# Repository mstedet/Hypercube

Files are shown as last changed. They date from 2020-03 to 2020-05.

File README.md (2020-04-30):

# Metalværksted Seniorhus Odense 3D printer  
## Baseret på Scott Alford's [HyperCube Evolution](https://www.thingiverse.com/thing:2254103)  

# Matrialer:
## [Item Aluminiumsprofiler 3030 and 2020 extrusion](https://www.linearmodul.dk/sida5_dk.html)
15 Meter [Profil 6 30x30 leicht, natur](https://product.item24.de/directlink/de/pro/41906)  
Profil 6 30x30 Let  
  * 4 stk 1500mm  
  * 10 stk 490mm  

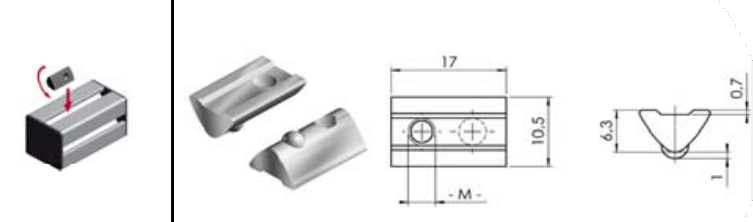
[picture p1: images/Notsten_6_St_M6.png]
Notsten 6 St M6
150 x [Notsten 6 St M6](https://www.linearmodul.dk/)   
50 x  Notsten Not 5, M5 svingbar m.skaft St.FZB  

100 x [Standard-Fastening Set 6 E, bright zinc-plated](https://product.item24.de/produkte/produktkatalog/produktdetails/products/standard-verbindungssaetze-1001012015/standard-verbindungssatz-6-e-verzinkt-64865/)   
 - Profil 6 30x30 Let kobling  
### item Konstruktionsprofile 5
[3 meter Profil 5 20x20, natur 0.0.370.03](https://product.item24.de/produkte/produktkatalog/produktdetails/products/konstruktionsprofile-5-1001042368/profil-5-20x20-natur-37003/)  
  
  * 2 stk 400mm  
  * 2 stk 440mm

## Bolte 
###  Button head screw, DIN EN ISO 7380-1  
   

#### M6
500 stk M6x12   

### DIN 912 ISO 4762 - Hexagon socket Head Cap Screws
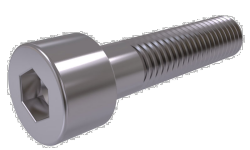
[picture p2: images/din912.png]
DIN 912
 
#### M5
8 stk M5x10, for Trapezewagon  
12 stk M5x10,  for Z-Axel Bearing  
#### M3
8 stk M3 x 10mm, for Z-Motor_Holder  
8 stk M3 x 12mm, for Trapezewagon  
24 stk M3 x 25mm, for Z-Axel Bearing  
8 stk M3 x 25mm, for Z-Axel Bracket

### DIN 965, SKRUE MED UNDERSÆNKET HOVED MED H-KRYDSKÆRV  
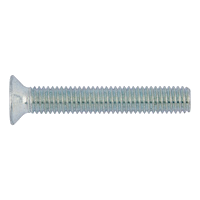
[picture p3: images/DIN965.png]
DIN965

#### M4
4 stk M4 x 50mm, for heatbed leveling 
## Møtriker
48 stk M3

## Axeler 
1 Meter [Aksel ø8  h6 - Hærdet & slebet dia.  8 mm (HL=6m)](https://www.linearmodul.dk/)  
1 Meter [Aksel ø10 h6 - hærdet & slebet dia. 10 mm (HL=6m)](https://www.linearmodul.dk/)  
4 Meter [Aksel ø12 h6 - hærdet & slebet dia. 12 mm (HL=6m)](https://www.linearmodul.dk/)  

## Motors
5 x [NEMA 17 42mm Stepper Motors](https://www.amazon.de/gp/product/B07STSYWY6/ref=ppx_yo_dt_b_asin_title_o08_s00?ie=UTF8&psc=1)  
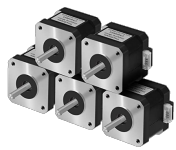
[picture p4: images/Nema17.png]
nema17


## Lead Screw M8 
2 x [Leitspindel+CopperMutter+VertikallagerLager+Kupplung (1Set)](https://www.amazon.de/gp/product/B07LDZPSKL/ref=ppx_yo_dt_b_asin_title_o06_s02?ie=UTF8&psc=1)  
[her er andre modeller fra aliexpress.com](https://www.aliexpress.com/item/32507277503.html?spm=a2g0o.cart.0.0.331e3c00jh9G45&mp=1) 
  
eller   

2 x [CNC 3D Printer THSL-300-8D Trapezoidal Rod T8 Lead Screw Thread 8mm Lead 1mm Length 600mm with Brass Nut](https://www.aliexpress.com/item/32507277503.html?spm=a2g0o.cart.0.0.590f3c00qjklE0&mp=1)  
4 x [KP08 Bearing Shaft Support Spherical Roller Zinc Alloy Mounted Bearings Pillow Block Housing](https://www.aliexpress.com/item/32571310602.html?spm=a2g0o.cart.0.0.590f3c00qjklE0&mp=1)  
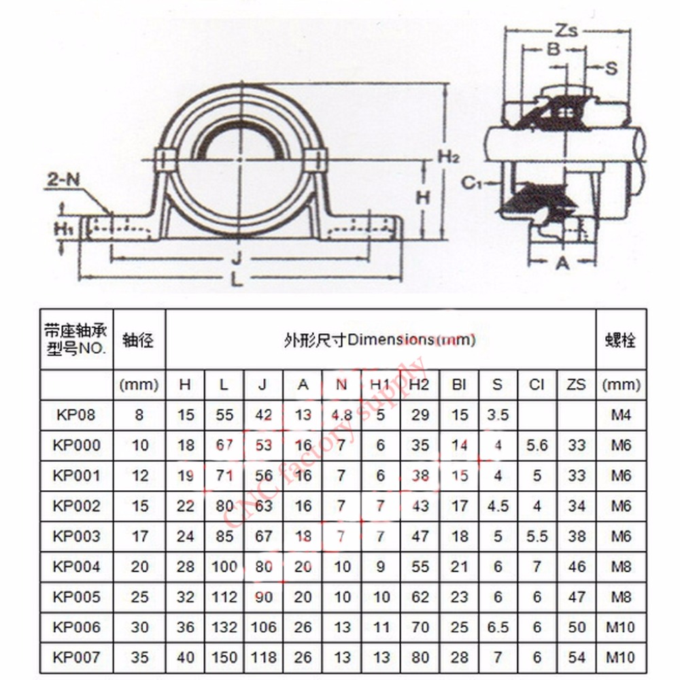
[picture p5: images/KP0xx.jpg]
KP0xx
  

## Pulleys and Belts
5m Polyurethane GT2 6mm belt &   
2 x [GT2 Timing Pulley (20 teeth) 5mm bore for 6mm belt](https://www.amazon.de/gp/product/B06XKVX3FY/ref=ppx_yo_dt_b_asin_title_o08_s00?ie=UTF8&psc=1)  
6 x [GT2 Idler Pulley (20 teeth) 3mm bore](https://www.amazon.de/gp/product/B07K8FNGCZ/ref=ppx_yo_dt_b_asin_title_o06_s01?ie=UTF8&psc=1)  
2 x [GT2 Idler Pulley without teeth (20 teeth) 3mm bore](https://www.amazon.de/gp/product/B083RCTF7T/ref=ppx_yo_dt_b_asin_title_o05_s00?ie=UTF8&psc=1)  

## Linear Bearings  
8 x LM12UU 12mm Linear Ball Bearings  eller [Linear Ball Bearings LM12LUU 12 Part Bush Bushing 3D Printers Parts Aluminum Accessories](https://www.aliexpress.com/item/4000586376717.html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,searchweb201602_,searchweb201603_)  
4 x LM10UU 10mm Linear Ball Bearings or 2 x LM10LUU 10mm Long Linear Ball Bearings  
4 x LM8UU 8mm Linear Ball Bearings  

## Heated Bed components
1 x [Print Bed Rubber Heater 408 x 408 mm](https://3dstore.dk/tilbehoer/reservedele/creality-3d/cr10s/print-bed-rubber-heater-408-x-408-mm/)  
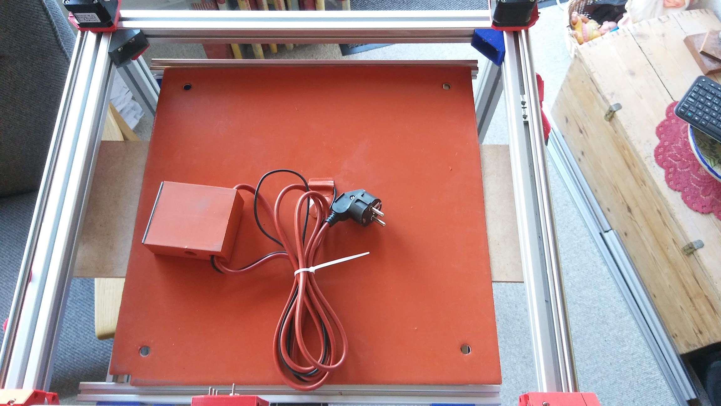
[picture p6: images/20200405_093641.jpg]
Heated Bed
  
1 x [PrimaCreator FlexPlate PEI 410 x 410 mm](https://3dstore.dk/tilbehoer/print-surface/primacreator-flexplate-pei-410-x-410-mm/)  
1 x Aluplate 430x430x3 mm  
1 x Flex pe coated plade - MGLo63.00.15 P1908084  
1 x [Hvid Magnetfolie. Selvklæbende. 50 cm](https://www.boxdelux.dk/shop/hvid-magnetfolie-selvklaebende-20277p.html)  
10 x [Type A - Hot bed platform leveling spring length 25mm outer diameter 10mm ID 5mm ](https://www.aliexpress.com/item/33001295923.html?spm=a2g0s.9042311.0.0.26194c4dYd3kvQ)
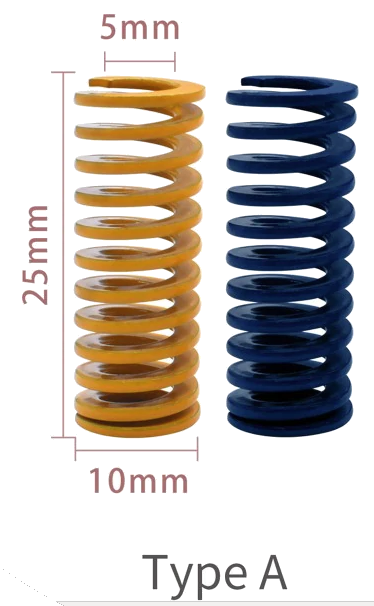
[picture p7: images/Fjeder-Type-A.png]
Fjedr-Type-A


## HotEnd:
1 x [E3D v6 HotEnd Full Kit - 1.75mm Bowden (24v)](https://filament23d.dk/e3d-v6-hotend-full-kit-1-75mm-bowden-24v-da.html) - **[Assembly Guid](https://wiki.e3d-online.com/E3D-v6_Assembly)**  
1 x [24V Blow 50mm](https://filament23d.dk/24v-blow-50mm-da.html)  
1 x [Extruder](https://www.amazon.de/gp/product/B07TJ8PB7D/ref=ppx_yo_dt_b_asin_title_o07_s00?ie=UTF8&psc=1  eller 
1 x [Aluminum Upgrade Dual Gear Mk8 Extruder for Extruder CR10 CR-10S PRO RepRap 1.75mm 3D Parts Drive Feed double pulley](https://www.aliexpress.com/item/4000103596931.html?spm=a2g0s.9042311.0.0.26194c4dYd3kvQ)  
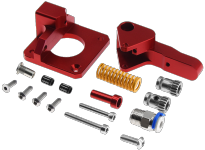
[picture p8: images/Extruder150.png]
Extruder


)  
10 stk [POWER MAGNET, SKIVE 12X6 MM](https://www.magnetz.dk/power-magnet-skive-12x6-mm)

## Control System
1 x [24V 400W power supply](https://www.amazon.de/gp/product/B01G257UHW/ref=ppx_yo_dt_b_asin_title_o02_s00?ie=UTF8&psc=1)  
1 x [BIGTREETECH-SKR-V1.4](https://github.com/bigtreetech/BIGTREETECH-SKR-V1.3/tree/master/BTT%20SKR%20V1.4)  
1 x [BIGTREETECH-TFT35-V3.0](https://github.com/bigtreetech/BIGTREETECH-TFT35-V3.0)  
1 x [BIGTREETECH-MINI-UPS-V2.0](https://github.com/bigtreetech/BIGTREETECH-MINI-UPS-V2.0/tree/master/BTT%20UPS%2024V%20V1.0)  
5 X [BIGTREETECH-TMC2130-V3.0](https://github.com/bigtreetech/BIGTREETECH-TMC2130-V3.0)  
1 x [ESP-01S WIFI Module ESP8266 For SKR](https://www.biqu.equipment/products/esp-01s-wifi-module-esp8266-for-skr-pro)  

# 3D-Printede Dele: 
## Filament:
2 x [Spectrum Filaments – PLA – 1.75mm – Deep Black – 1 kg](https://3dstore.dk/filament/spectrum-filaments-pla-1-75mm-deep-black-1-kg/)  
2 x [Spectrum Filaments – PLA – 1.75mm – Dark Grey – 1 kg](https://3dstore.dk/filament/spectrum-filaments-pla-1-75mm-dark-grey-1-kg/)  
2 x [Spectrum Filaments – PLA – 1.75mm – Navy Blue – 1 kg](https://3dstore.dk/filament/spectrum-filaments-pla-1-75mm-navy-blue-1-kg/)  
2 x [Spectrum Filaments – PLA – 1.75mm – Bloody Red – 1 kg](https://3dstore.dk/filament/spectrum-filaments-pla-1-75mm-bloody-red-1-kg/)  
## PrintaFix:
3 x [APRINTAPRO PrintaFix Basic 100ml](https://3dstore.dk/tilbehoer/printafix/aprintapro-printafix-basic/)  
## Filer:
* [FreeCad (FCStd) filer & STL filer kan hentest her](https://github.com/mstedet/Hypercube/tree/master/FreeCad)  
## 3030 Profiler
4 x EndCap_3030 - **[STL-fil](/FreeCad/3030/EndCap_3030.stl)** - **[FreeCad-fil](/FreeCad/3030/EndCap_3030.FCStd)**
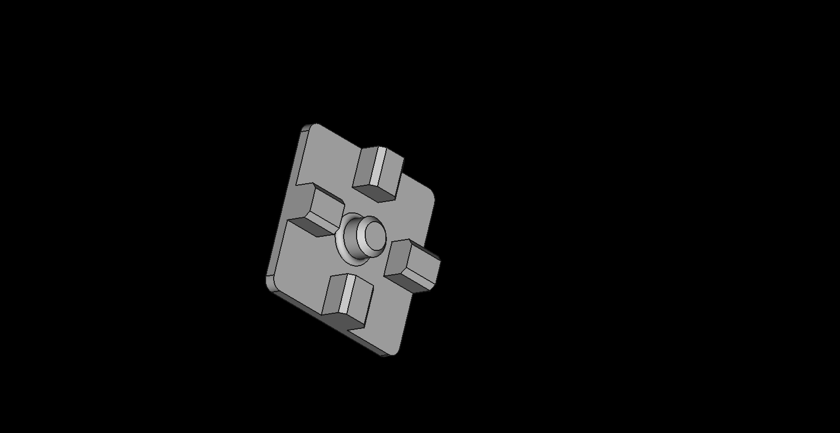
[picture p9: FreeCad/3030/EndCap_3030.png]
EndCap_3030
 
4 x FodBund 3030 - **[STL-fil](/FreeCad/3030/Foot-30a.stl)** - **[FreeCad-fil](/FreeCad/3030/Foot-30a.FCStd)**
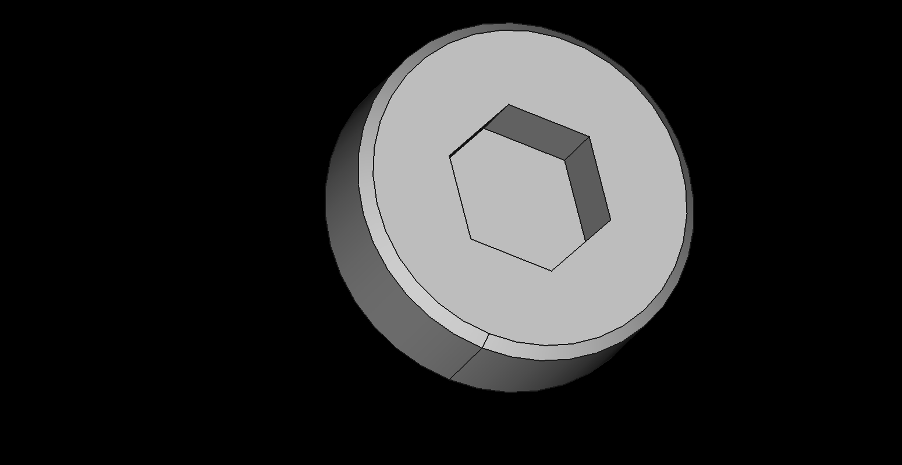
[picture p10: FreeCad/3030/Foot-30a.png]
FodBund
 
4 x FodJustermøtrik - **[STL-fil](/FreeCad/3030/Foot-30b.stl)** - **[FreeCad-fil](/FreeCad/3030/Foot-30b.FCStd)**
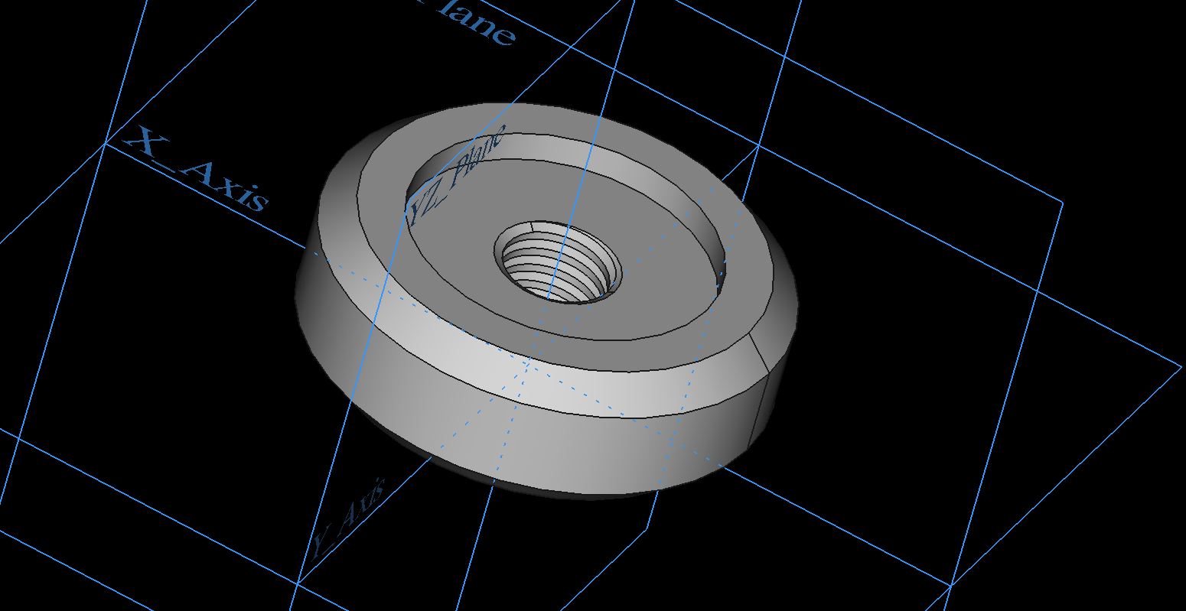
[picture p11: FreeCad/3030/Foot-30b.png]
FodJustermøtrik
 

## X-Axel
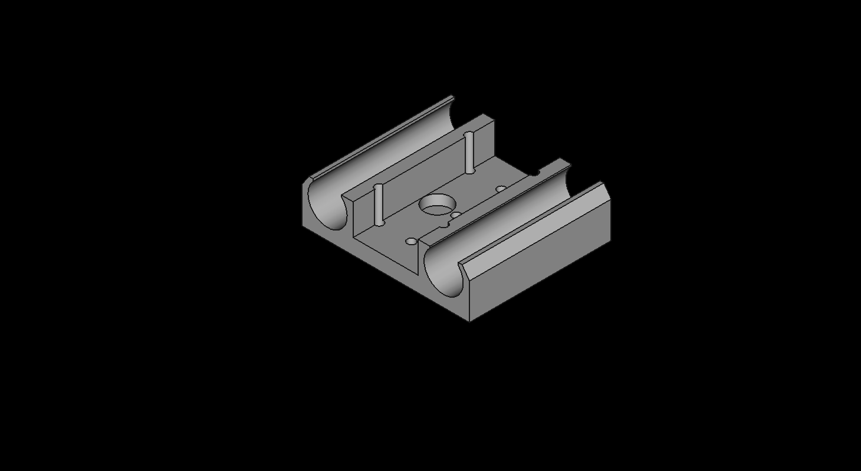
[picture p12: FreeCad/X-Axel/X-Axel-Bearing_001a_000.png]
X-Axel-Bearing_A
1 x X-Axel-Bearing_A   
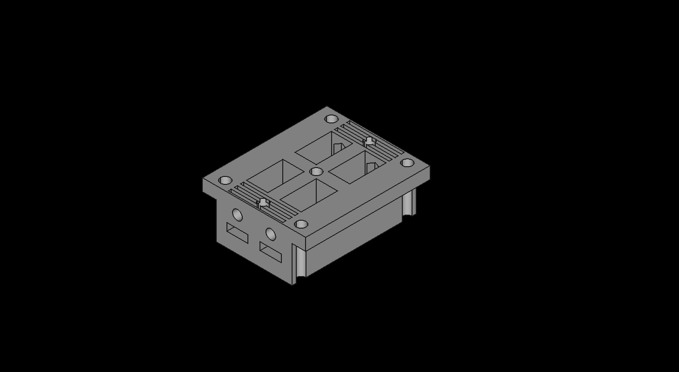
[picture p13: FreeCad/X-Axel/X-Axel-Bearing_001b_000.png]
X-Axel-Bearing_B
1 x X-Axel-Bearing_B   
2 x X-Axel-Belt-Tension  
1 x X-Axel-Printhead-Base

## Y-Axel
2 x Afstandstykke_2mm - **[STL-fil](/FreeCad/Y-Axel/Afstandstykke_2mm/Afstandstykke_2mm.stl)** - **[FreeCad-fil](/FreeCad/Y-Axel/Afstandstykke_2mm/Afstandstykke_2mm.FCStd)**
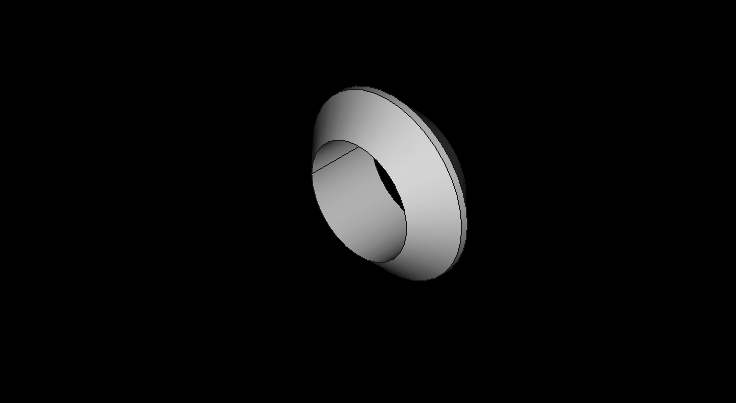
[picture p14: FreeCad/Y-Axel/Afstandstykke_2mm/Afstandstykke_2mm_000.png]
Afstandstykke
  
2 x Y-Axel-Bearing_A - **[STL-fil](FreeCad/Y-Axel/Y-Axel-Bearing_007/Y-Axel-Bearing_007a.stl)** - **[FreeCad-fil](/FreeCad/Y-Axel/Y-Axel-Bearing_007/Y-Axel-Bearing_007a.FCStd)**
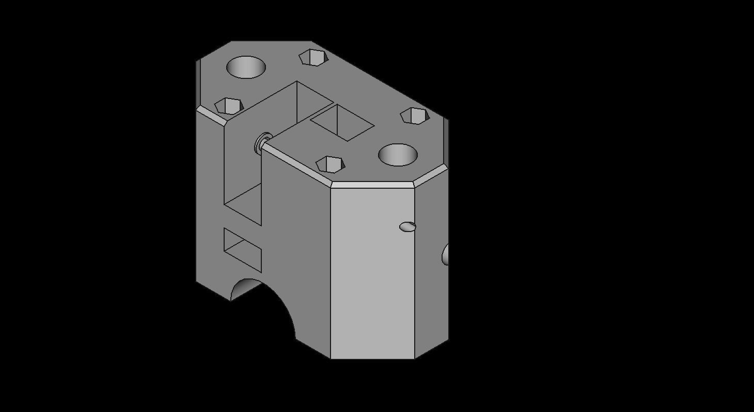
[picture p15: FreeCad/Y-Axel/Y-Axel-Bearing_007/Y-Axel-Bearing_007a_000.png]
Y-Axel-Bearing_A
 
2 x Y-Axel-Bearing_B  - **[STL-fil](FreeCad/Y-Axel/Y-Axel-Bearing_007/Y-Axel-Bearing_007b.stl)** - **[FreeCad-fil](/FreeCad/Y-Axel/Y-Axel-Bearing_007/Y-Axel-Bearing_007b.FCStd)**
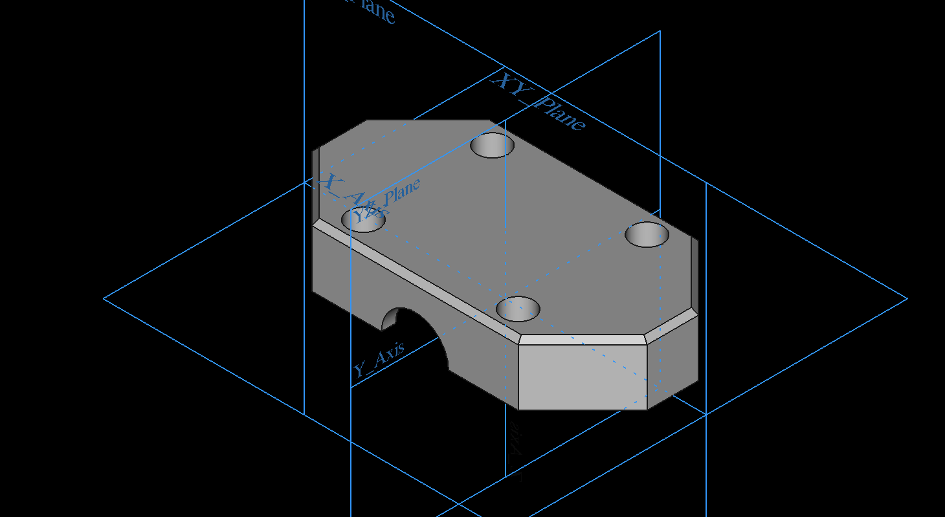
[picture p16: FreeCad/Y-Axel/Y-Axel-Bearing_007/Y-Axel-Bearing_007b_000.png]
Y-Axel-Bearing_B
 

## Z-Axel
* 4 x Z-Axel-Bearing part a  
  * 2 x venstre  
  * 2 x højre (venstre spejlet i cura)  

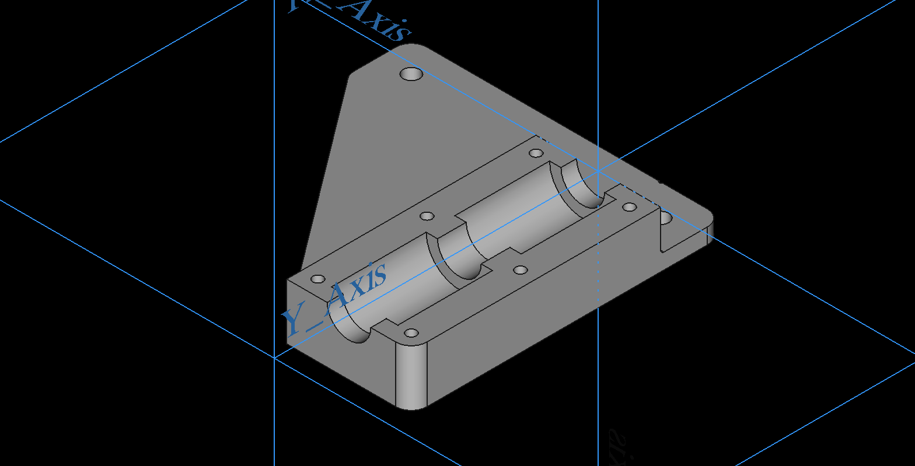
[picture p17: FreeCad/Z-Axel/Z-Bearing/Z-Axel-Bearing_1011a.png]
Z-Axel-Bearing_1011a
  

* 4 x Z-Axel-Bearing part b  

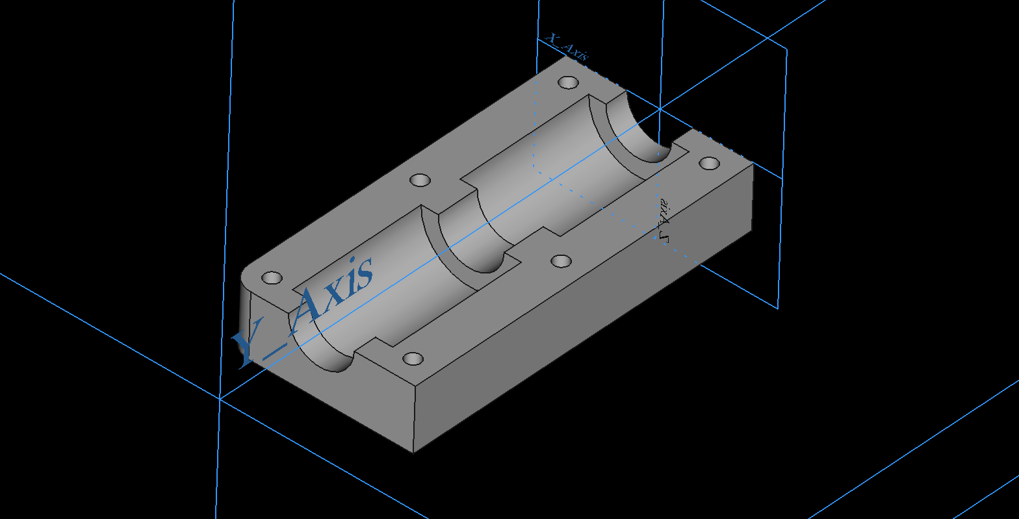
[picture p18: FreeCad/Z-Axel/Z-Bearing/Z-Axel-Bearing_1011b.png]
Z-Axel-Bearing_1011b
  

* 8 x Z-Bracket  
  * 4 x venste  
  * 4 x højre (venstre spejlet i cura)  

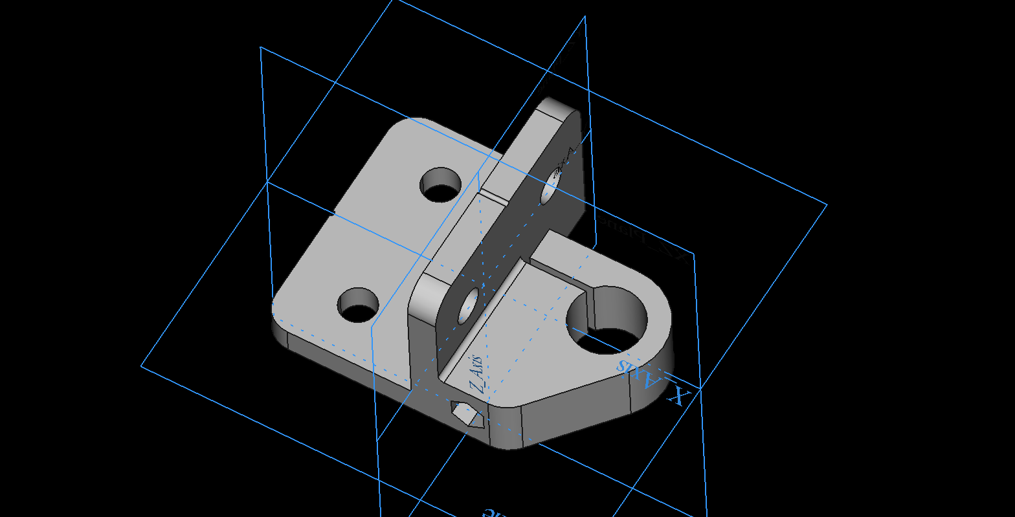
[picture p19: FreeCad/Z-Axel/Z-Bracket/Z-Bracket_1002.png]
Z-Bracket_1002
  

* 2 x Z-KP08_Holder  

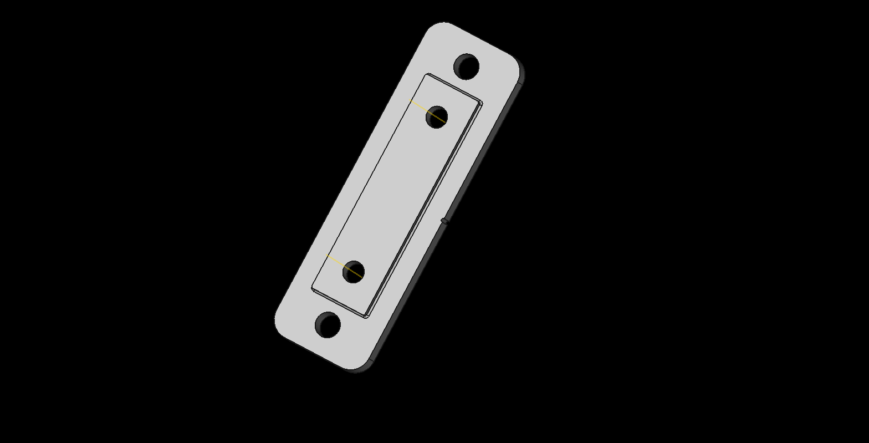
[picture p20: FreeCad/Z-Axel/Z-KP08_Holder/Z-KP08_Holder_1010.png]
Z-KP08_Holder_1010
  

* 2 x Z-Motor_Holder  

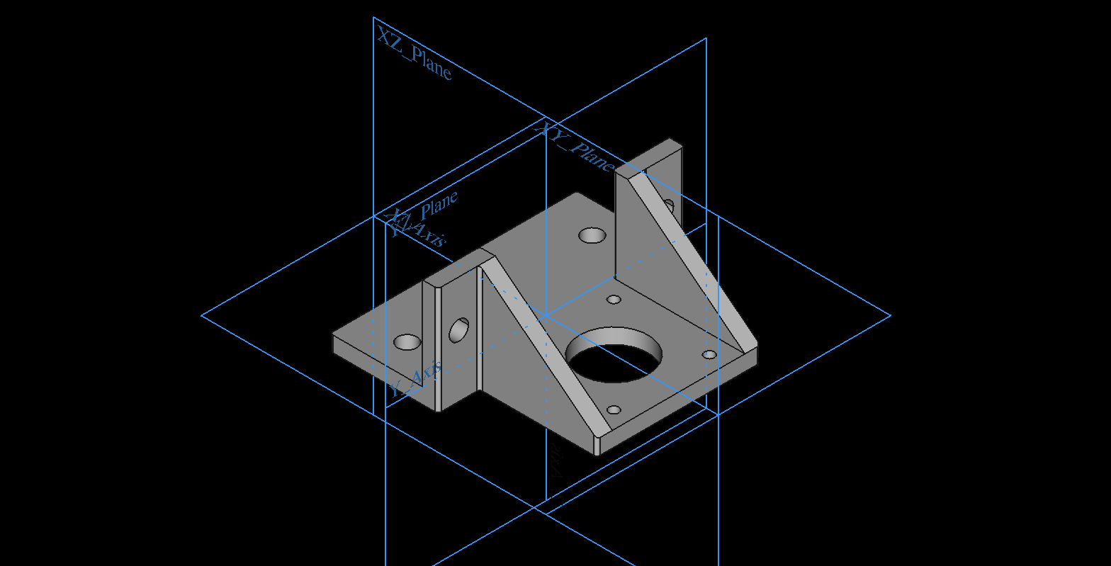
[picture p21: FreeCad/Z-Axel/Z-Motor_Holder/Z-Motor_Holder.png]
Z-Motor_Holder
  

* 2 x Trapezewagon  

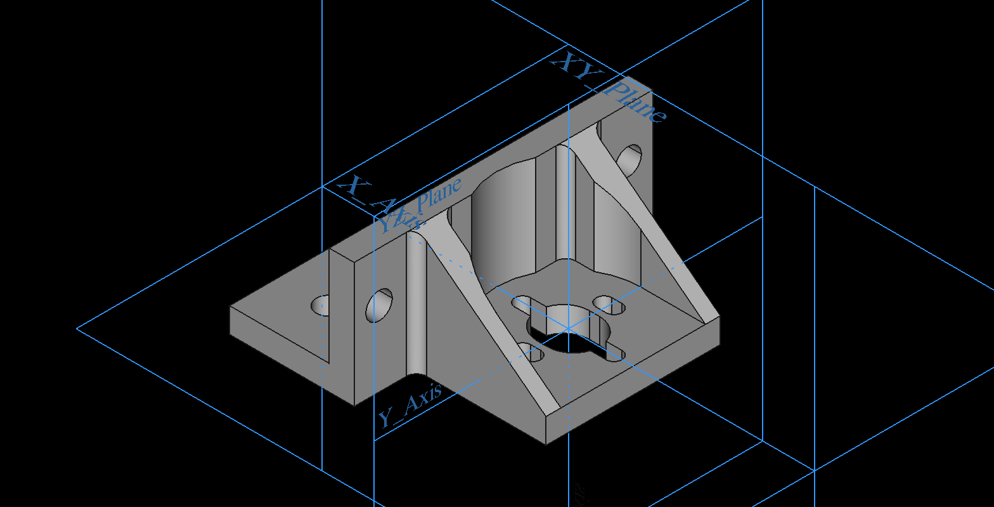
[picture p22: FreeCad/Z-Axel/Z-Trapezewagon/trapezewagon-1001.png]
trapezewagon-1001
  

## Drag Chain
1 x Chain Start  
20 x Chain Top - **[STL-fil](/FreeCad/DragChain/DragChainTop_22.5.stl)** - **[FreeCad-fil](/FreeCad/DragChain/DragChainTop_22.5.FCStd)** 
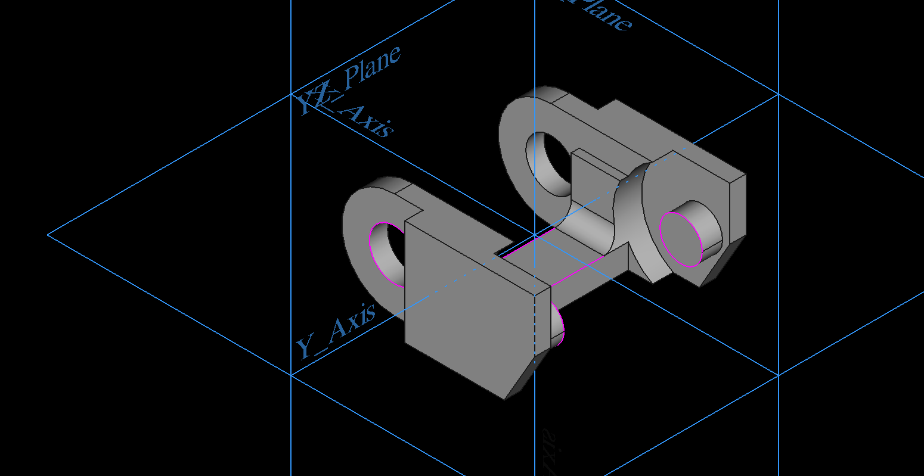
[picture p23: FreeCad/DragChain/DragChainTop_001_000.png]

20 x Chain Bund - **[STL-fil](/FreeCad/DragChain/DragChainBund_22.5.stl)** - **[FreeCad-fil](FreeCad/DragChain/DragChainBund_22.5.FCStd)**
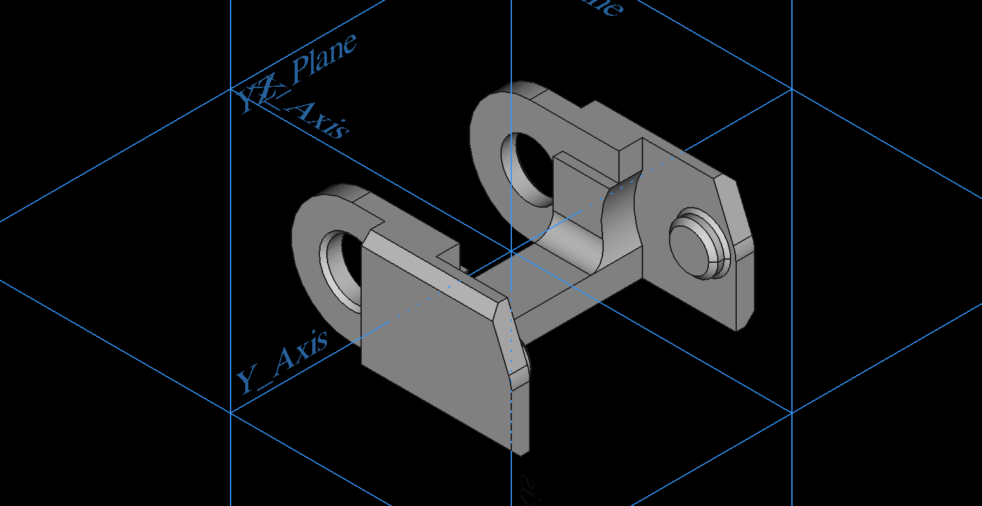
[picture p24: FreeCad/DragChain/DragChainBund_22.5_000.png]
DragChainBund_22.5
 
1 x Chain Slut  

# Firmware
* [MarlinFirmware/Marlin](https://github.com/MarlinFirmware/Marlin)
* [MarlinFirmware/Configurations](https://github.com/MarlinFirmware/Configurations/tree/import-2.0.x/config/examples/Creality)  
* Video 
  * [Ender 3 (Pro) Marlin 2 0 Installation Upgrade - Updated Version](https://www.youtube.com/watch?v=RbbzsJBpEhc&t=154s)  
  * [Easily upgrade the Marlin firmware on your kit 3D printer!](https://www.youtube.com/watch?v=lAKyZd63_ns)
 
# Calibrate
## Calibrate the Extruder
* DrVax
  * [Calibrate Your 3d Printer Extruder](https://www.youtube.com/watch?v=lRoCwxRZsvU)
  * [Calibrating your Extruder and Adjusting Flow Rate](https://docs.google.com/presentation/d/1wpuLDlLARoFbS7apN1uDdRoSiFpWugTFrTnqUJ-ni_s/edit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)
* Thomas Sanladerer
  * [How To Calibrate the Extruder Steps (Ender-3 / Ender-5 / CR-10)](https://letsprint3d.net/how-to-calibrate-the-extruder-steps-ender-3-5-cr-10/)
## Printing Speed
* Thomas Sanladerer
  * [3D printing guides - Tuning speeds](https://www.youtube.com/watch?v=7HsIZuj9vOs)  
## Using Marlin's PID autotune
* Thomas Sanladerer
  * [3D printing guides - Using Marlin's PID autotune](https://www.youtube.com/watch?v=APzJfYAgFkQ)

# Customize Marlin LCD
  * [Thinkyhead Software Video](https://www.youtube.com/watch?v=3fGHgzZqaGs)
  * [Marlin Bitmap Converter](https://marlinfw.org/tools/u8glib/converter.html)

# Configuration af BTT SKR v1.4 Turbo
* Chris Riley
  * [BigTreeTech SKR v1.4 Mainboard - Full Install Part 1 - 2209 Drivers - Chris's Basement](https://www.youtube.com/watch?v=oHMZ0ocTYvM)
  * [BigTreeTech SKR v1.4 Mainboard - Full Install Part 2 - 2209 Drivers - Chris's Basement](https://www.youtube.com/watch?v=j2FL_mY_LsY&t=1219s)
  * [VSCODE - Edit Marlin Firmware - How To - Chris's Basement](https://www.youtube.com/watch?v=W6zYvRgGr3Q)
* Teaching Tech
  * [Bigtreetech SKR V1.4 (Turbo) comprehensive guide](https://www.youtube.com/watch?v=-Gdk0wHg51w)
  * [BTT TFT35 dual mode touch screen guide](https://www.youtube.com/watch?v=l1Putn10_Ek)
  * [Add wifi to your Bigtreetech mainboard/touchscreen - ESP-01S guide](https://www.youtube.com/watch?v=AGTF-JEUHNA)

# Tips and Triks
## indsæt magneter i print
Kilde: [Pause print in gcode ](https://forum.prusaprinters.org/forum/original-prusa-i3-mk2-s-others-archive/pause-print-in-gcode/#p125758)  

Video: [Embedded Magnets Thanks to Flipping Normals!](https://www.youtube.com/watch?v=oF1SdIR-Kow)

Code:
```
G1 X10.000 Y200.000 E0; parking position GET THE PRUSA TO STICK IT'S TONGUE OUT! (edited to revise Y coordinate)
M0 Indsæt magnet ; user stop
G28 X Y ; Home x y aksel
M105; return to current temp
```

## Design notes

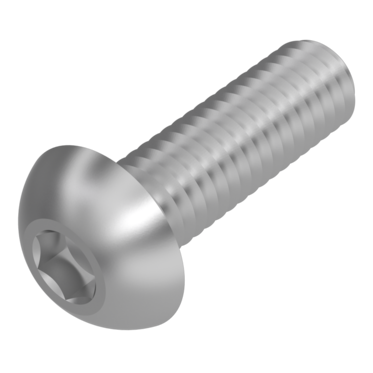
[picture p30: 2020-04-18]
images/ISO-7380-1-Flachkopfschraube-Edelstahl-A2-70.Vollbild.png

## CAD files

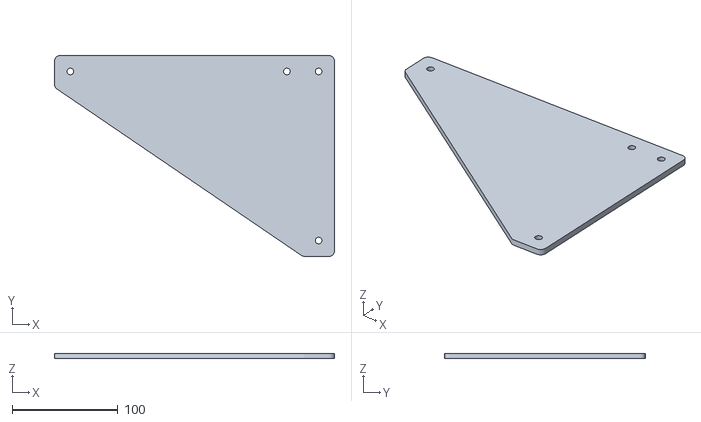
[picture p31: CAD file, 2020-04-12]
FreeCad/3030/265x190_Trekant.stl
265.0 x 190.0 x 5.00

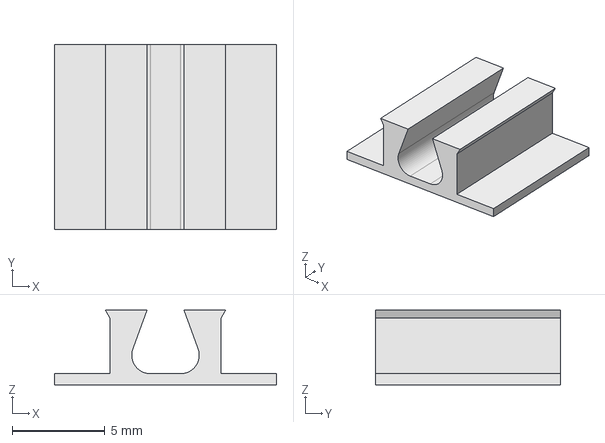
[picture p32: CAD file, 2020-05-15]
FreeCad/3030/KabelCover/KabelCover.FCStd
12.0 x 10.0 x 4.03 mm

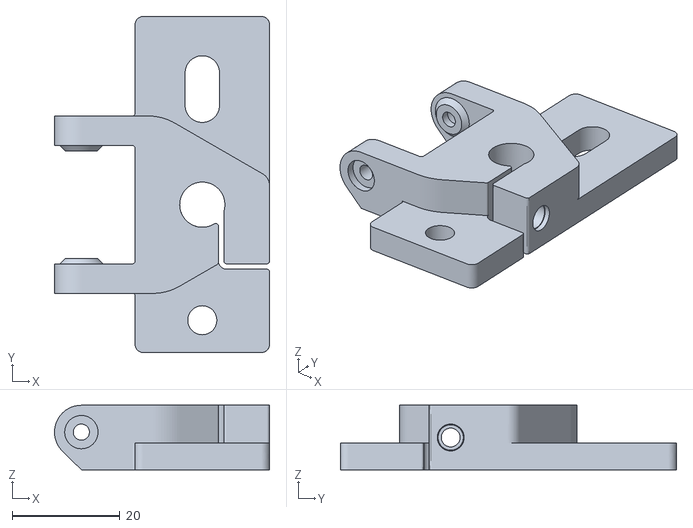
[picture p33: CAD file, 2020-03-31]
FreeCad/by SCOTT/XY-Idler-Mount/XY_Idler_Mount_-_Right_yDia8_-_1.1.stl
40.0 x 62.5 x 12.0

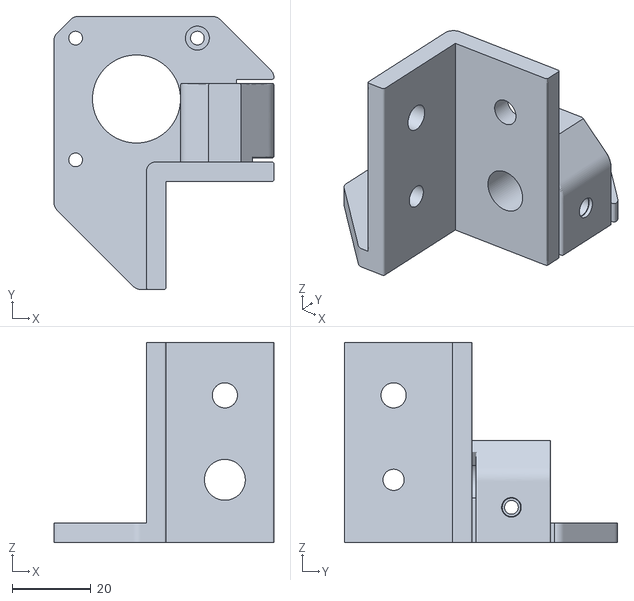
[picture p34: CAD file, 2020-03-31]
FreeCad/by SCOTT/XY-Stepper-Mount/XY_Stepper_Mount_-_Right_-_1.0.stl
56.0 x 69.5 x 51.0

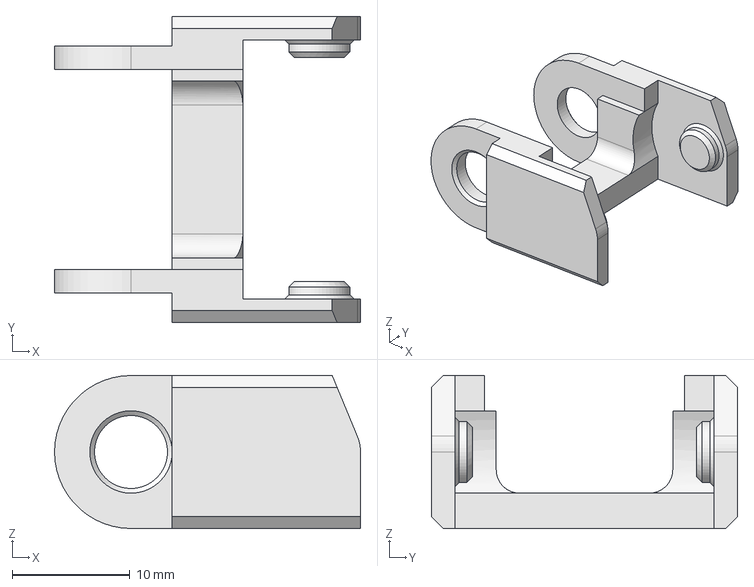
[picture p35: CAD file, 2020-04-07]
FreeCad/DragChain/DragChainBund_22.5.FCStd
26.0 x 26.0 x 13.0 mm

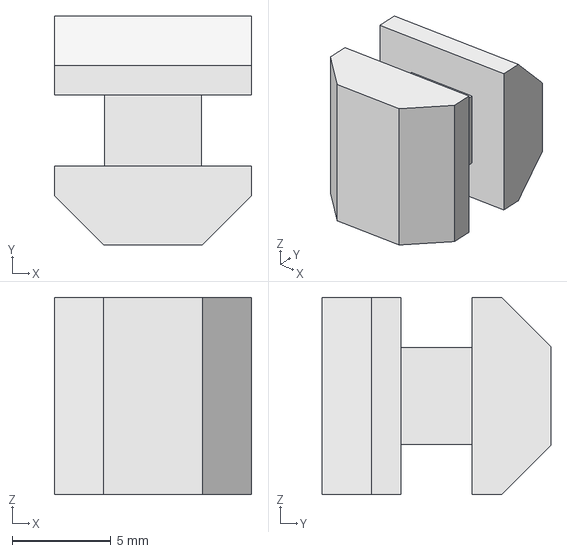
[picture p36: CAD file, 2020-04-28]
FreeCad/HeatBed/2020/2020_Samling.FCStd
10.0 x 11.6 x 10.0 mm

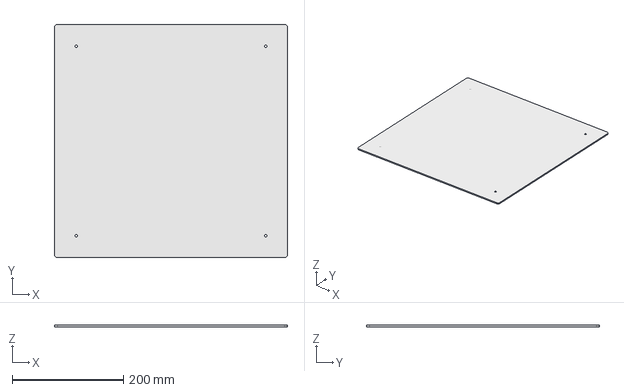
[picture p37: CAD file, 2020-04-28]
FreeCad/HeatBed/Alu-HeatBed-001.FCStd
418.0 x 418.0 x 3.00 mm

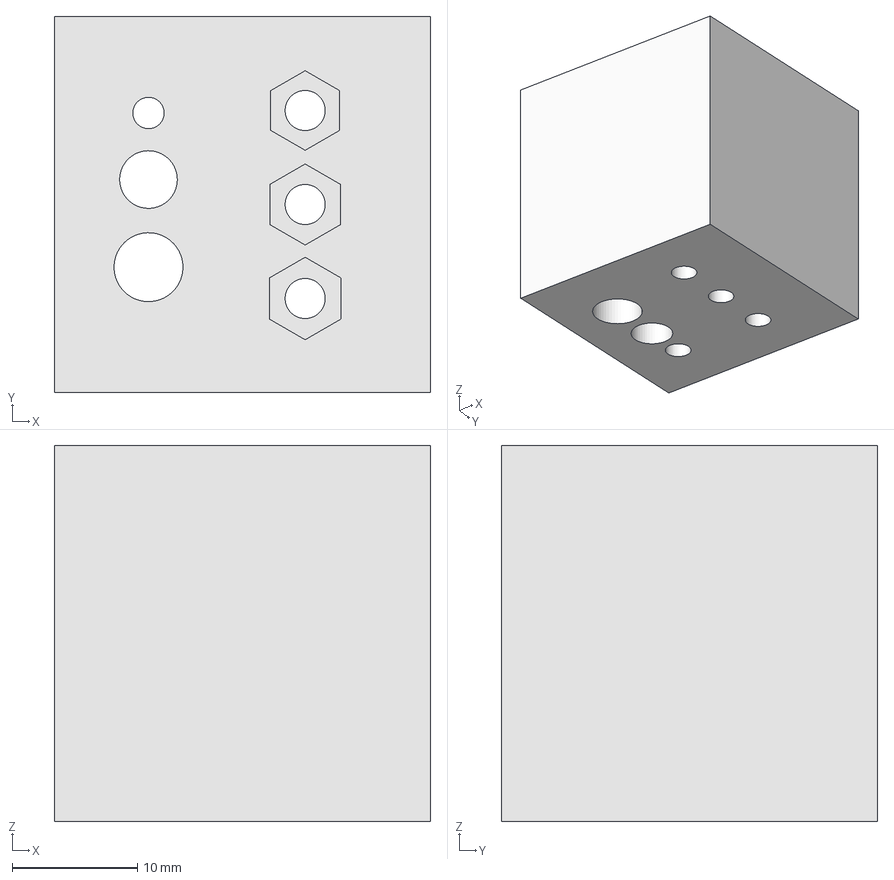
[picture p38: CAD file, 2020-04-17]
FreeCad/Test_Cube/Test_Cube.FCStd
30.0 x 30.0 x 30.0 mm

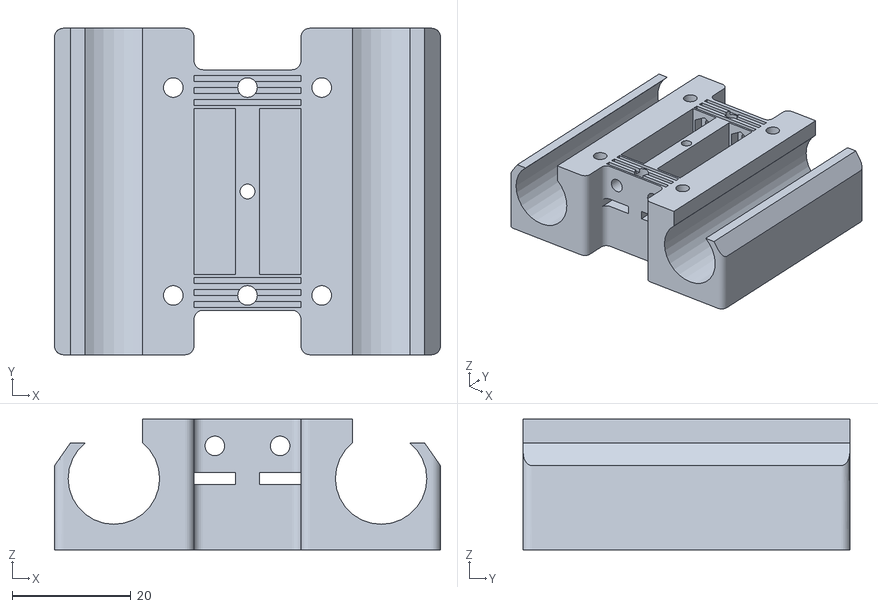
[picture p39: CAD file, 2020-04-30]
FreeCad/X-Axel/X-Axel-Bearing_1000_003.stl
65.0 x 55.0 x 22.0

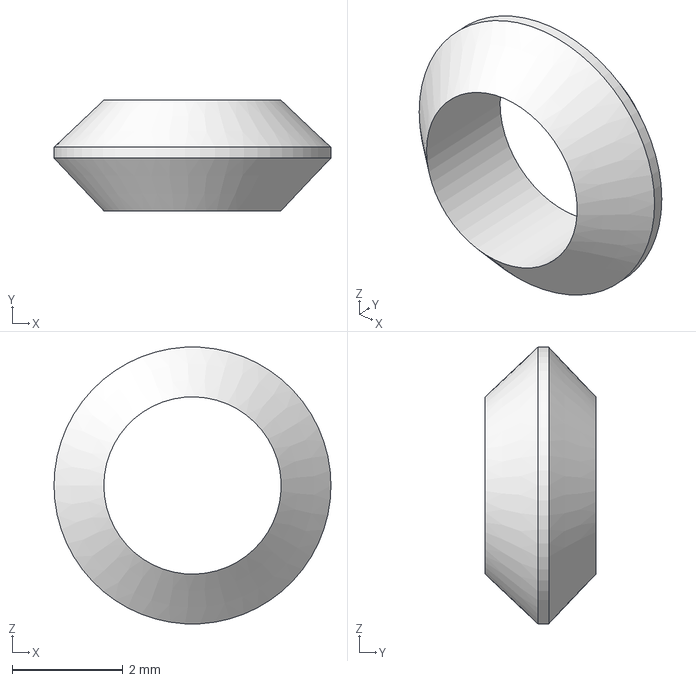
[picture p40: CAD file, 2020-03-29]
FreeCad/Y-Axel/Afstandstykke_2mm/Afstandstykke_2mm.FCStd
5.00 x 2.00 x 4.99 mm

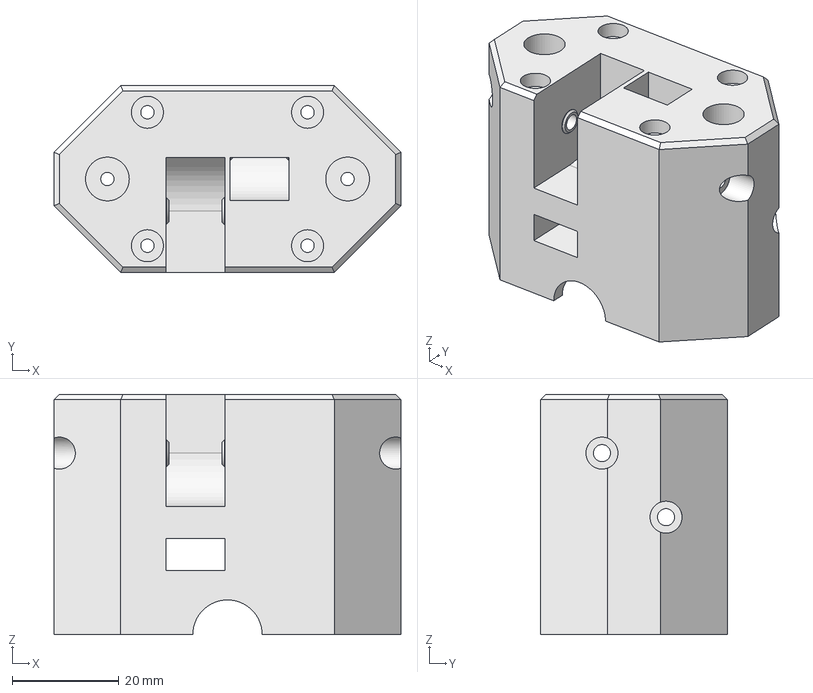
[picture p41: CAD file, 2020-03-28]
FreeCad/Y-Axel/Y-Axel-Bearing_006/Y-Axel-Bearing_006a.FCStd
65.0 x 35.0 x 45.0 mm

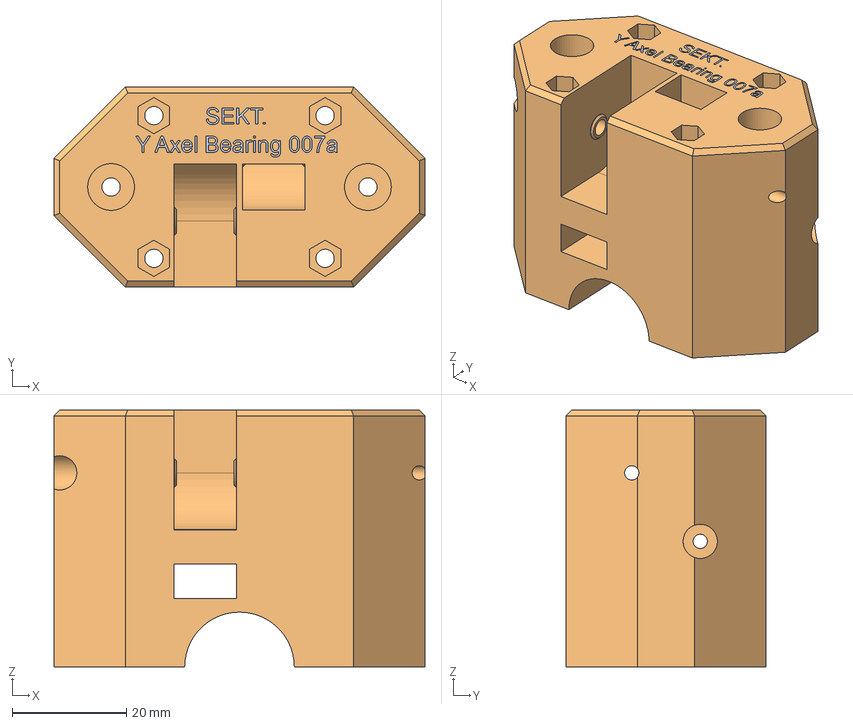
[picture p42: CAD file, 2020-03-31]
FreeCad/Y-Axel/Y-Axel-Bearing_007/Y-Axel-Bearing_008a.FCStd
65.0 x 35.0 x 45.0 mm

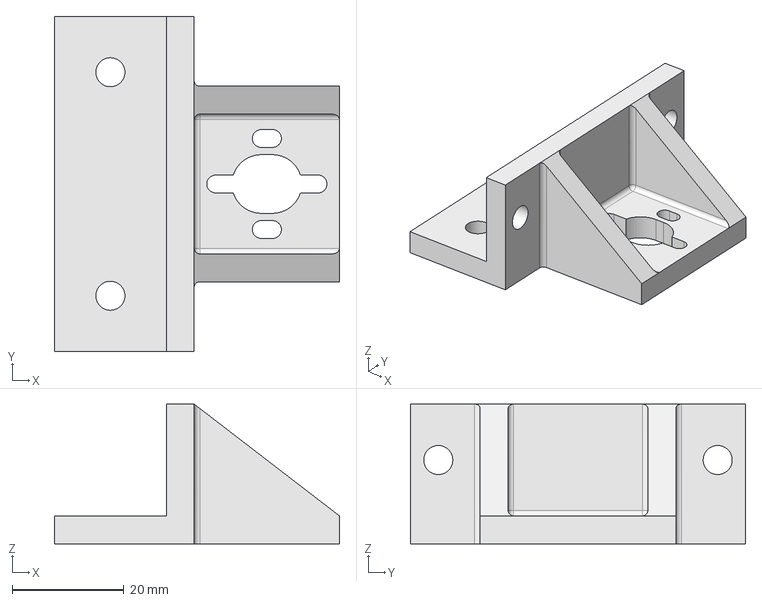
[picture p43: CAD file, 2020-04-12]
FreeCad/Z-Axel/trapezewagon/trapezewagon-002.FCStd
51.0 x 60.0 x 25.0 mm

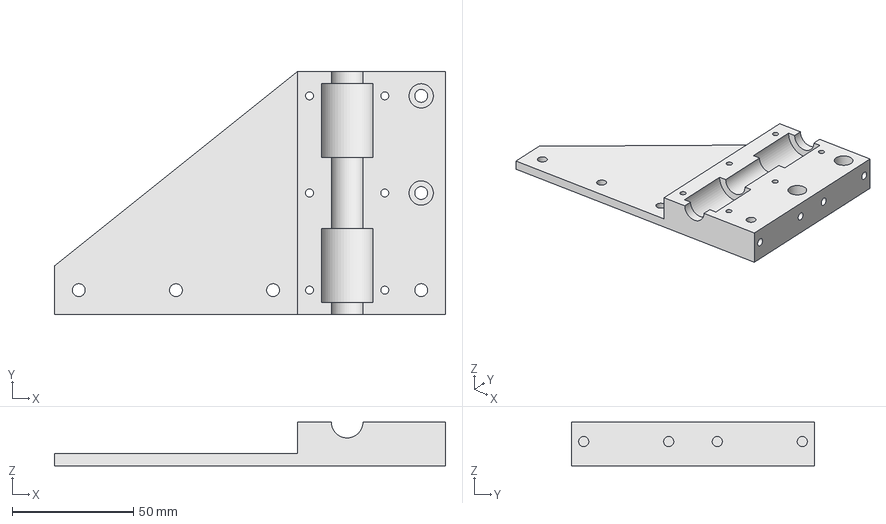
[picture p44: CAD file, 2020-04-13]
FreeCad/Z-Axel/Z-Axel-Bearing/Z-Axel-Bearing_032a.FCStd
161.0 x 100.0 x 18.0 mm

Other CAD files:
FreeCad/Z-Axel/Z-Axel-Bearing_020/Z-Axel-Bearing_030.FCStd
FreeCad/Z-Axel/Z-Bearing/Z-Axel-Bearing_1012a.FCStd
FreeCad/Z-Axel/Z-Bracket/Z-Bracket_1003.FCStd
FreeCad/Z-Axel/Z-Gear+Motor/GearAxel.FCStd
FreeCad/3030/150x150_Trekant.stl
FreeCad/3030/150x150_trekant.FCStd
FreeCad/3030/265x195_trekant.FCStd
FreeCad/3030/90x90_Trekant.stl
FreeCad/3030/90x90_trekant.FCStd
FreeCad/3030/EndCap_3030.FCStd
FreeCad/3030/EndCap_3030.stl
FreeCad/3030/Foot-30a.FCStd
FreeCad/3030/Foot-30a.stl
FreeCad/3030/Foot-30b.FCStd
FreeCad/3030/Foot-30b.stl
FreeCad/3030/KabelCover/kabelCover.stl
FreeCad/3030/Profile_3030-1490.FCStd
FreeCad/3030/Profile_3030-1490.stl
FreeCad/3030/Profile_3030-490.FCStd
FreeCad/3030/Profile_3030-490.stl
FreeCad/3030/Profile_3030.FCStd
FreeCad/DragChain/DragChainBund_22.5.stl
FreeCad/DragChain/DragChainTop_001.FCStd
FreeCad/DragChain/DragChainTop_001.stl
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

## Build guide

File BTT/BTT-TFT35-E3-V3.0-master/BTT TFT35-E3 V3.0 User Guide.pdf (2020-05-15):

Shenzhen BIGTREE Technology CO., LTD.

## BIG TREE TECH

# BIGTREETECH TFT35 V3.0

# User Guide

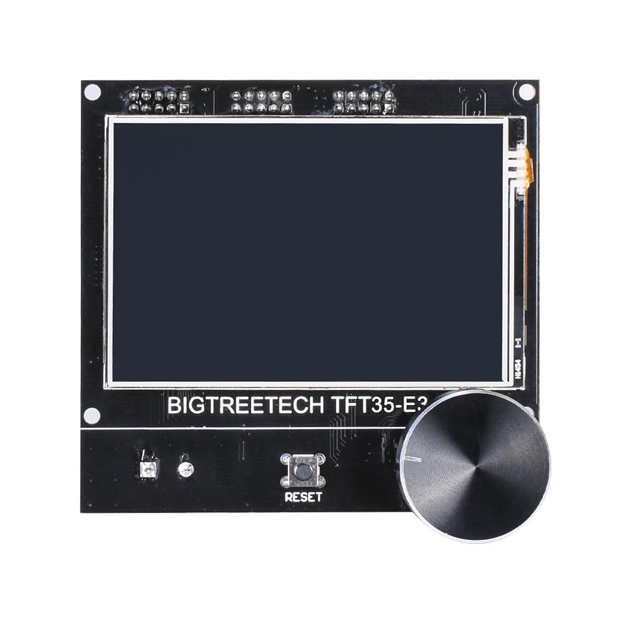
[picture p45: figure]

## BIG TREE TECH

# Ⅰ.Product Introduction

BIGTREETECH TFT35-E3 V3.0 is a medium size, dual-mode,

### ultra-clear 3D printing machine display launched by the 3D printing team

### of Shenzhen BIGTREE Technology CO., LTD., which can perfectly

replace the original LCD screen of Ender3 printer.

## 1.Product characters：

1）ARM Cortex-M3 series STM32F207VCT6 chip with 32-bit CPU 120MHz; 2）Upgrade the firmware by SD card. It is easy and convenient to operate. 3）This display board has higher compatibility. Users can select two work modes: UART serial port screen mode and 12864 screen mode.
4）Serial port screen mode supports two printing modes: SD card and U disk. 5）Reserve WIFI port, and WIFI function is realized by external WIFI module； 6）Reserve the extension port of filament breaking detection (FIL-DET)； 7）Reserve the extension port of automatic shutdown after printing (PS-ON);； 8）LCD12864 mode uses EXP1, EXP2 and EXP3. EXP1 and EXP2 are LCD screen ports of normal motherboard. EXP3 is the LCD interface used by E3 series motherboard (such as SKR MINI E3 V1.2, SKR E3 DIP V1.1, etc.) ；
9）TFT touch screen mode：serial port screen RS232 port；
10）2 sets of UART serial port extension ports are reserved for DIY use.

## 2.Product Parameters：

Appearance size：93*87mm
Installation size：Perfectly replace the original LCD screen of Ender3 printer， detail information please check TFT35-E3 V3.0 SIZE Microprocessor：STM32F207VCT6
Power Input：DC 5V
SD card logic voltage：3.3V and 5V（Such as: support MEGA2560 main control chip motherboard, higher compatibility)

# Ⅱ.Indicator Information

After the board is powered on：
Red light D6 is the power indicator: the red light is on, indicating normal power supply;
Green light D3 is SD card detection indicator: D3 is always on when the SD card inserted, and then off when SD card pulled out

## BIG TREE TECH

# Ⅲ.Ports on the board

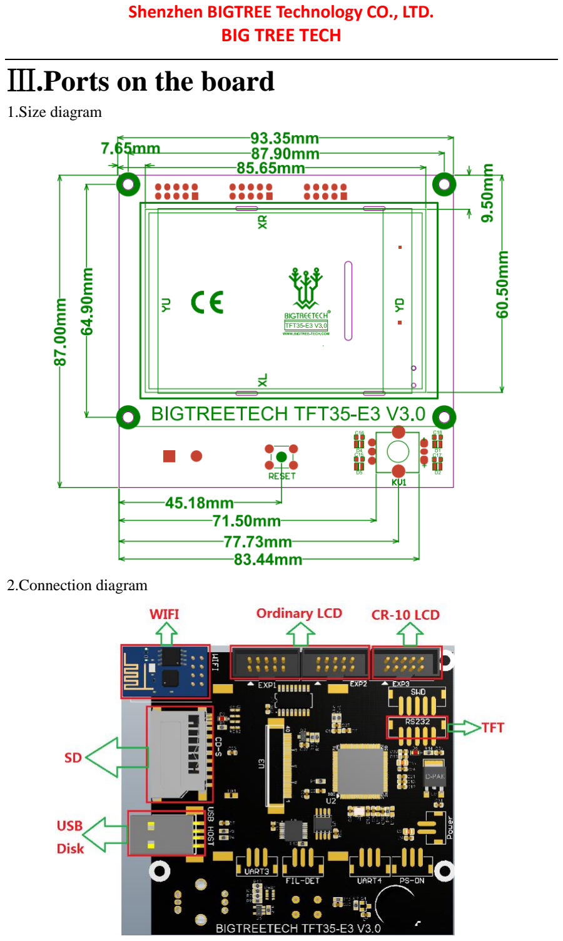
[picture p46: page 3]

1.Size diagram

2.Connection diagram

## BIG TREE TECH

Notes：
1. When using 12864 screen mode, connect the port EXP1 and EXP2 to the motherboard. There is no touch function in this mode.
2. When using serial port screen mode, connect with TFT or AUX-1 on the motherboard via RS232. This mode has touch function；
3. Two work modes can be changed by one key. Press the encoder about 3 seconds until the mode selection page appears, then press the encoder after selecting the mode.

# Ⅳ.Firmware Introduction

Factory board will be equipped with test firmware, it can be used directly. It can also be upgraded according to our company's open source website.
1. Ways to obtain the firmware of motherboard
Get it from customer service or technical staff；
Log in the open source website of our company to download ： https://github.com/bigtreetech
2. Firmware update
Firmware file name：：
BIGTREE_TFT35_V3.0. (version number).bin
First copy the above firmware to SD root directory, and then insert the card into the SD card slot of the board. Next please re-power the board or press the reset key, and wait for about 10 seconds before the update is completed.；
3. For DIY board firmware, please refer to the file TFT35-E3 V3.0PIN.

# Ⅴ.Notes：

## 1. The name of the firmware file in the SD card cannot

## be changed. (including capital and small letters)；

## 2.The wiring process must be carried out under the

## premise of power failure. The power can be put on after

## checking the correct connection of the circuit and the

## correct insertion of the drive. This prevents boards

and screens from burning up due to faulty wiring,

## causing unnecessary damage.；

## BIG TREE TECH

## 3.Pay attention to the wiring sequence and do

## not insert the wire inversely. Please refer to PIN

file for detailed line order.

### If you encounter other problems, please contact us, we will

### definitely answer your questions patiently; If you have any good

### suggestions on our products, please give feedback to us, we will

### consider them. Thank you for choosing BIGTREETECH products!

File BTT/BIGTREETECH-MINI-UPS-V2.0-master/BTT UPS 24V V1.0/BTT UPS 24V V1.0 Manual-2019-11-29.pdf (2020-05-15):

Shenzhen BIGTREE Technology co., LTD.

## BIG TREE TECH

# BIGTREETECH UPS 24V V1.0

# Module Instruction

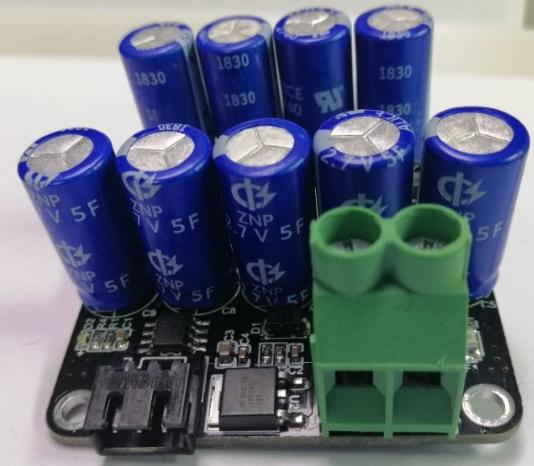
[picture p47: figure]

## BIG TREE TECH

# Ⅰ、Introduction：

### BTT UPS 24V V1.0 is an external module of 3D printer with the

### function of power off resume print, which was launched by 3D printing

### team of Shenzhen Big Tree Technology CO., LTD. It is applicable to all

3D printers powered by DC24V switch power, such as Ender 3 printer.

## 1. Feature：

1）Adopt voltage comparator LM393 chip, which can detect power failure sensitively;
2）Equipped with 9 2.7V 5F super capacitors to store electricity, so that there is sufficient power supply after detecting the power failure, then the printer can successfully complete the corresponding operation.
3）An anti-reverse protection circuit is added at the power interface to prevent irreversible damage caused by the reverse power supply, which greatly protects the circuit board;
4）The module is small and easy to install;
5）Main function: realize the power off resume print function;

## 2. Module parameters：

External dimension：52.53*50mm
Installation dimensions：44.58mm*39.38mm
Power input：DC24V
Logic voltage：3.3V or 5V
Support model：All DC24V powered 3D printers are available（like Ender3） Item drawing：

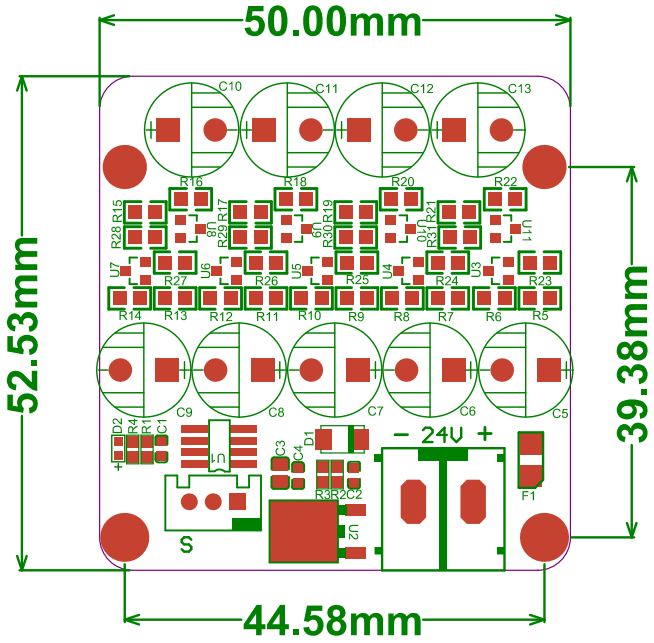
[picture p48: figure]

## BIG TREE TECH

# Ⅱ、Module power-on

After BTT UPS 24V V1.0 power on, D2 red light in the lower left corner will go on, indicating normal power supply.
Note: The input power only supports DC24V. Please pay attention to distinguish the positive and negative poles when wiring. The wiring process must be carried out in the state of power failure and confirm the wiring is correct before power on. Our company will not be responsible for any loss caused by wiring.

# Ⅲ、Module communicates with the printer's

# motherboard

### BTT UPS 24V V1.0 communicates with the motherboard through

### XH2.54mm 3P plug-in wire. Please identify the position of signal line "S"

### when wiring. Only when the signal line and the motherboard signal line

### interface are properly connected can the power off resume print function

be realized.

Wiring picture：

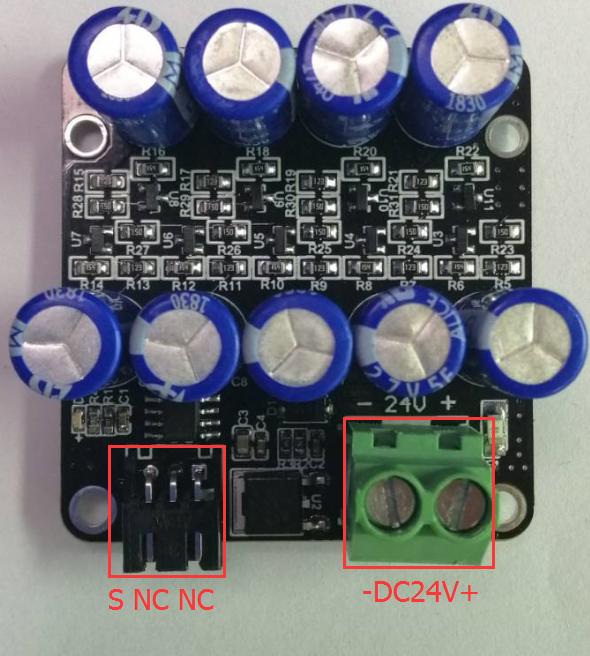
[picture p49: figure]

## BIG TREE TECH

# Ⅳ、Firmware description

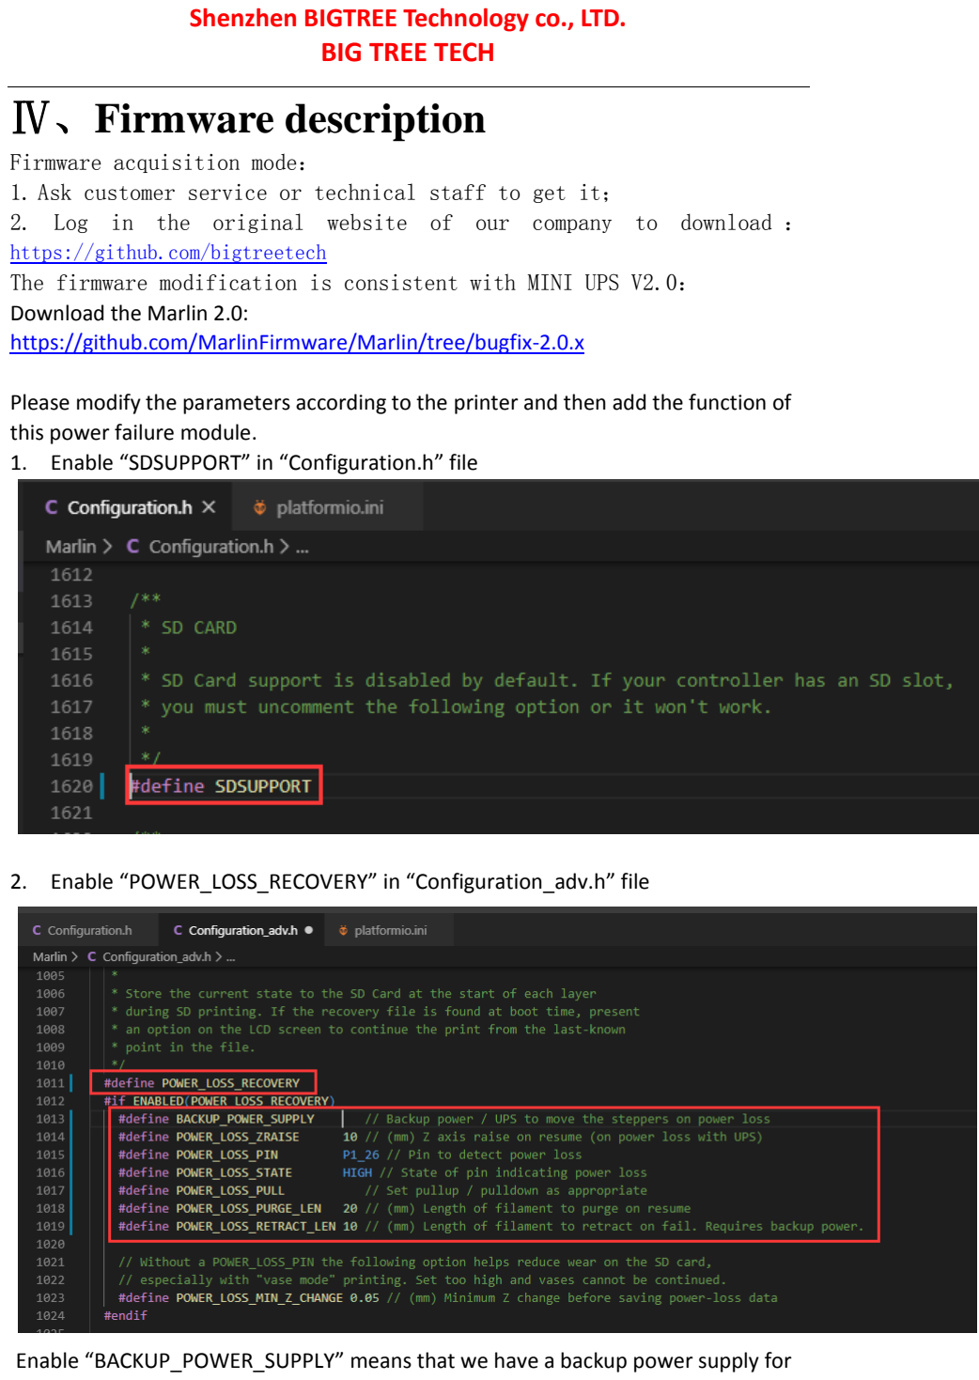
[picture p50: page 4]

Firmware acquisition mode：
1. Ask customer service or technical staff to get it；
2. Log in the original website of our company to download ： https://github.com/bigtreetech
The firmware modification is consistent with MINI UPS V2.0： Download the Marlin 2.0:
https://github.com/MarlinFirmware/Marlin/tree/bugfix-2.0.x

Please modify the parameters according to the printer and then add the function of this power failure module.
1. Enable “SDSUPPORT” in “Configuration.h” file
2. Enable “POWER_LOSS_RECOVERY” in “Configuration_adv.h” file

Enable “BACKUP_POWER_SUPPLY” means that we have a backup power supply for

## BIG TREE TECH

the stepper so that the hotend can leave the printed model when power failed. “POWER_LOSS_ZRAISE” is the height of Z-axis rise when power failed. “POWER_LOSS_PIN” is the GPIO port to which the module is connected, Modify “P1_26” to the GPIO to which the module is actually connected.

## Ⅴ、Notes

1. This module only supports DC24V power supply.

## Please confirm that your printer is powered by DC24V

## power supply before installation；

## 2. When connecting the power cord, please

## distinguish the positive and negative poles; when

## connecting the signal line "S", connect the signal

## lines on the motherboard correctly.；

3. All wiring must be done in case of power failure.

## Only after all wiring is confirmed to be correct can

power on.

### If you encounter other problems, please contact us, we will

### definitely answer your questions patiently; If you have any good

### suggestions on our products, please give feedback to us, we will

### consider them. Thank you for choosing BIGTREETECH products!

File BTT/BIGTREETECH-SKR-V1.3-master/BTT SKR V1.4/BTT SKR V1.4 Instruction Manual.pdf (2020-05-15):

Shenzhen Big Tree Technology CO.,LTD .

## BIG TREE TECH

# BIGTREETECH SKR V1.4

# Motherboard Operating instruction

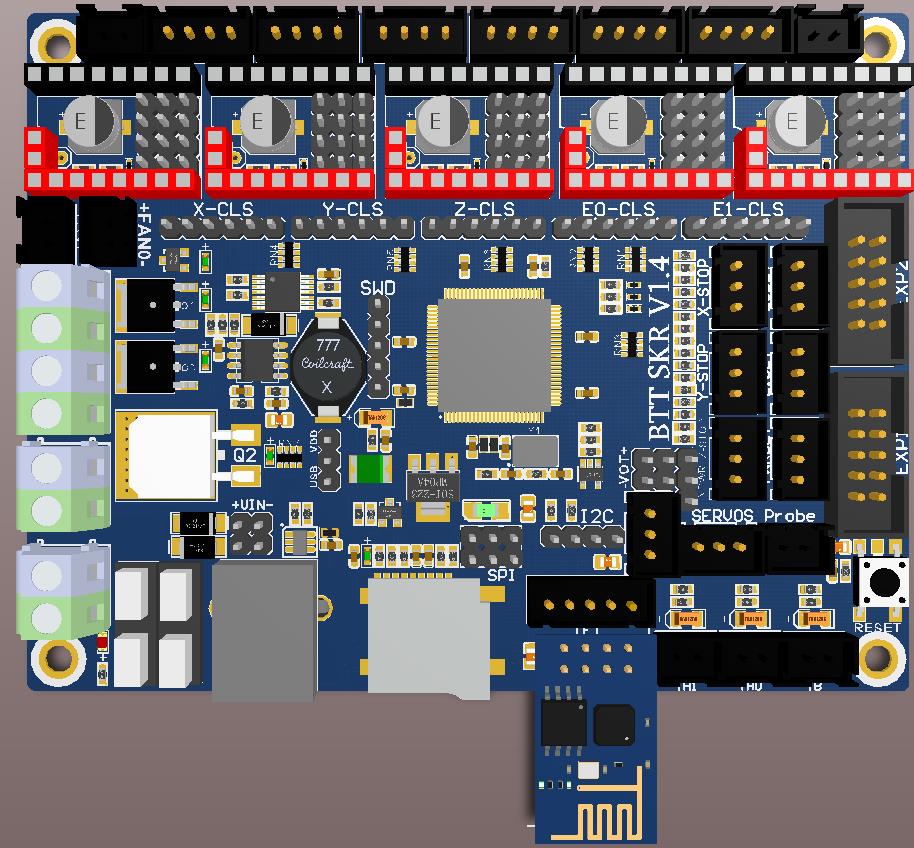
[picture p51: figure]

## BIG TREE TECH

# Ⅰ.Product Introduction

### BIGTREETECH SKR V1.4 motherboard is a 32-bit 3D printer

### motherboard optimized and upgraded by the 3D printing team of

### Shenzhen Big Tree Technology CO., LTD. for the deficiencies of V1.3

version, especially suitable for small and medium-sized printers.

## 1.SKR Motherboard Features:：

1）Using 32-bit main frequency 100MHz ARM level Cortex-M3 series LPC1768 main control chip, the performance has been greatly improved;
2）Equipped with highly modular and open source firmware Marlin2.0, which is convenient for users to DIY and secondary development;
3）Using dedicated power chip M6130, support 12-24V power input; 4）Support 2.4, 2.8, 3.5 inch color touch screen, support LCD2004 screen, LCD12864 screen；
5）Upgrade and configure the firmware through SD card, which is simple, convenient and efficient;
6）The SPI and UART working mode driven by the TMC driver, also having the DIAG pin, which eliminates complex wiring process and can be used by simple unplugging jumper cap;
7）Support Resume Printing While Power Off, Filament Break Detection, Automatic Shutdown After Printing and so on；
8）High performance MOSFET tube, better heat dissipation effect; 9）Using removable fuse makes the replacement process easier;
10）Reserved extended port SERVOS and Probe to support BL Touch;； 11）Support RGB Neopixel light bar；
12）Use the power selection design to separate the USB power supply from the switch power supply, effectively avoiding the situation that the USB port of the computer is burnt out due to short circuit;
13）The special function interface uses the row needle with conspicuous color, which greatly reduces the error rate of wiring.
14）I2C, SPI and WIFI interfaces are reserved for convenience of DIY; 15）Closed-loop drive interface is reserved to reduce the trouble of plug-in switching module；
16）Double z-axis interface, eliminating the trouble of external drive expansion module;
17）The thermistor interface is protected by a bile capacitor pressurized resistor to enhance the resistance of the interface；
18）More fan interfaces: 1 way CNC fan, 3 way normally open fan;

## BIG TREE TECH

19）Plug-in external DC5V power supply module to supply power to TFT screen, BLtouch and Neopixel.

## 2. SKR Motherboard Parameters:：

Appearance size: 110*85mm
Mounting size: 102*76mm
Microprocessor: ARM Cortex-M3 CPU Input voltage: DC12V-DC24V 5A-15A
Logic voltage：DC 3.3V
WIFI module：ESP-01S
Motor driver: Support TMC5161、TMC5160、TMC2209、TMC2225、TMC2208、 TMC2130、ST820、LV8729、DRV8825、A4988 etc., independent external motor drive.
Driver working mode support: SPI、UART、STEP/DIR
Motor driver interface：X、Y、Z、E0、E1，5 way（Each has a closed loop drive interface) up to 256 subdivisions
Temperature sensor interface: TH0, TH1, TB, 3 channel 100K NTC Temperature sensor interface: TH0, TH1, TB, 3 channel 100K NTC (thermal resistance) Display：2.4、2.8、3.5 inch TFT（Support dual mode screen）、LCD2004、 LCD12864
PC communication interface: Square USB, easy to plug, communication baud rate of 115200
Expand the interface function support: Resume Printing While Power Off, Filament Break Detection, Automatic Shutdown After Printing, Automatic leveling, BL Touch
Support file format: G-code
Supported machine architecture: XYZ、delta、kossel、Ultimaker、corexy Recommended software: Cura、Simplify3D、pronterface、Repetier-host、 Makerware

# Ⅱ.SKR Motherboard Electricity:

After the SKR mainboard is powered up, the D5 red light in the lower left corner will go on, indicating normal power supply. The 5V SEL in the middle of the board is the power selection terminal；

1）When using USB to power the motherboard：

2）When using 12v-24v power supply：

## BIG TREE TECH

# Ⅲ.SKR Motherboard and Computer

# Connection

SKR motherboard communicates with the computer through the [USB] interface. The computer needs to install the driver program first and then insert the motherboard into the computer to identify the port for data transmission. Without installing the driver, it is easy for the computer to fail to recognize the USB port.
Using the Marlin2.0 firmware, follow the tutorial for installation:

tutorial：https://www.dropbox.com/s/ppjfflhf3j5yzh2/MarlinV2.0%20SKRV1.1%20instruction.docx?dl=0driver：https://www.dropbox.com/s/a0k5idjmf4fn82f/lpc176x_usb_driver.inf?dl=0

# Ⅳ.SKR Motherboard and Interface

# Instruction

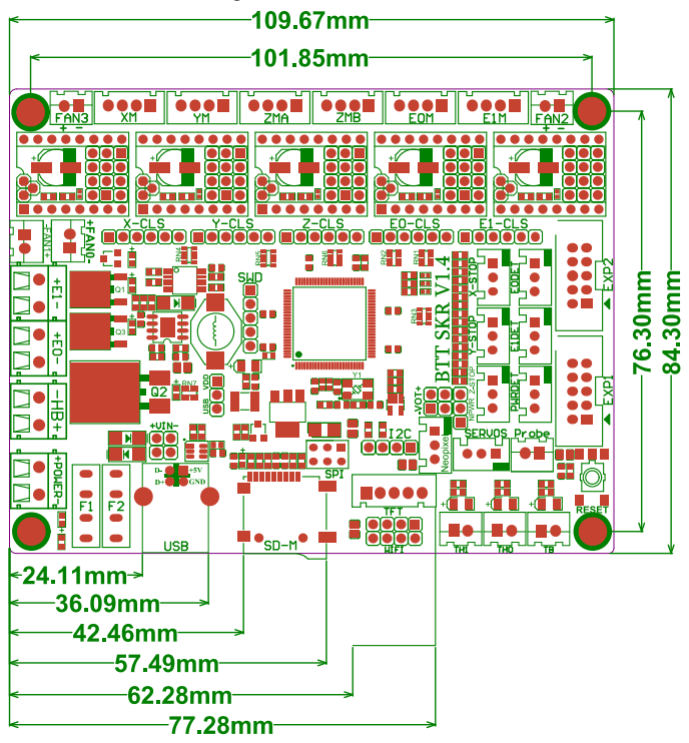
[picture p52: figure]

1. SKR Motherboard Size Diagram

## BIG TREE TECH

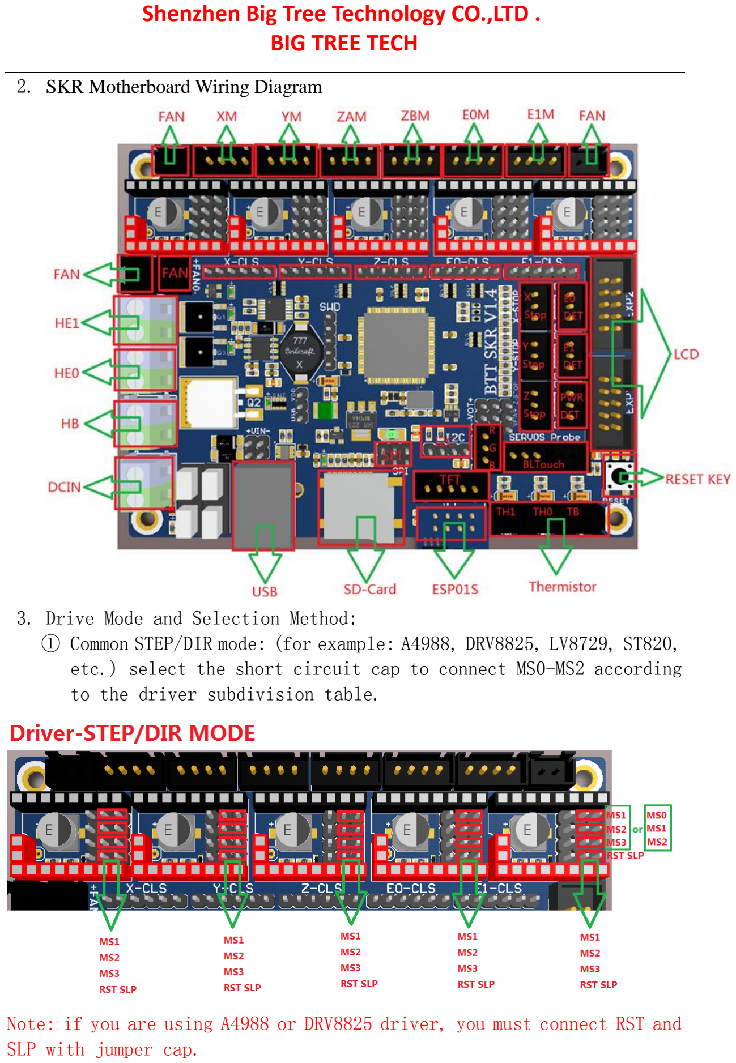
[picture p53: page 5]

2. SKR Motherboard Wiring Diagram
3. Drive Mode and Selection Method:
① Common STEP/DIR mode: (for example: A4988, DRV8825, LV8729, ST820, etc.) select the short circuit cap to connect MS0-MS2 according to the driver subdivision table.

Note: if you are using A4988 or DRV8825 driver, you must connect RST and SLP with jumper cap.

## BIG TREE TECH

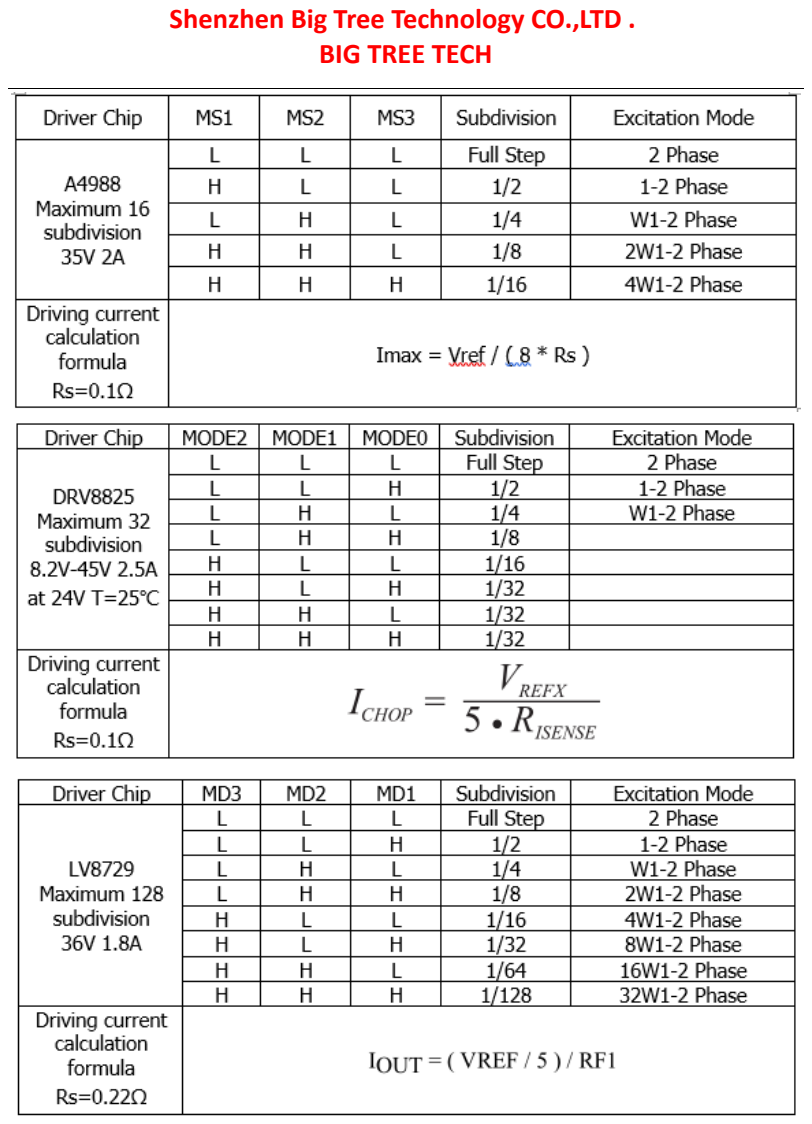
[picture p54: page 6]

## BIG TREE TECH

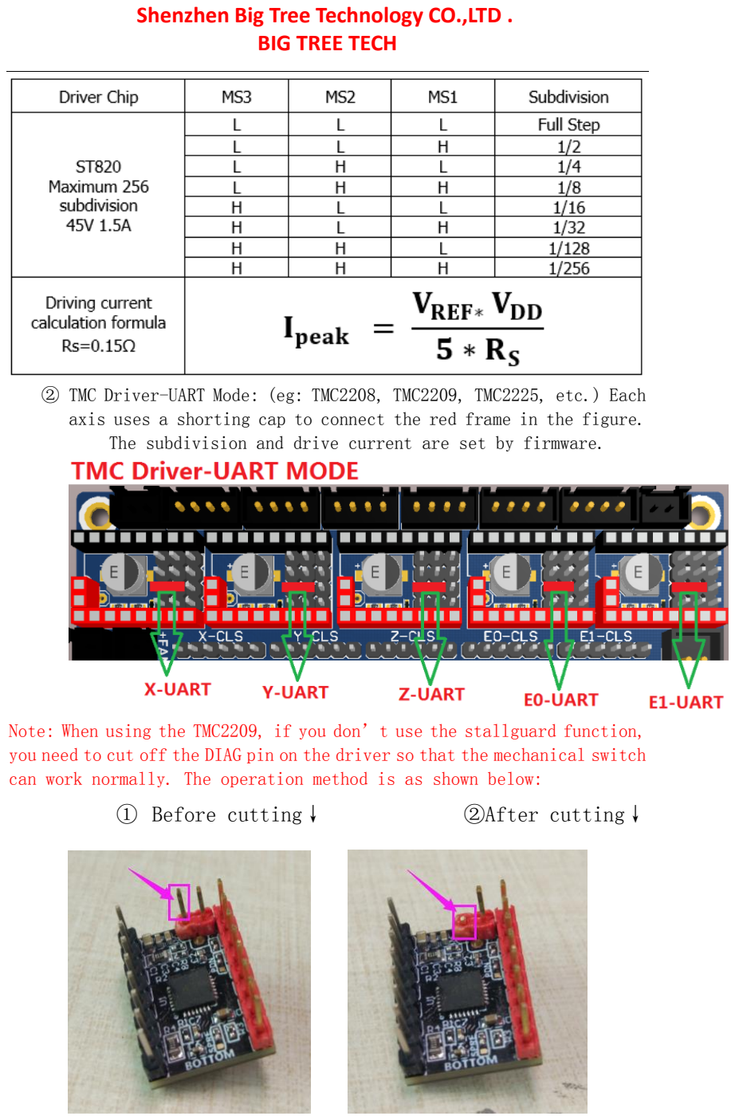
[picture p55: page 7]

② TMC Driver-UART Mode: (eg: TMC2208, TMC2209, TMC2225, etc.) Each axis uses a shorting cap to connect the red frame in the figure. The subdivision and drive current are set by firmware.

Note: When using the TMC2209, if you don’t use the stallguard function, you need to cut off the DIAG pin on the driver so that the mechanical switch can work normally. The operation method is as shown below:
① Before cutting↓ | ②After cutting↓

## BIG TREE TECH

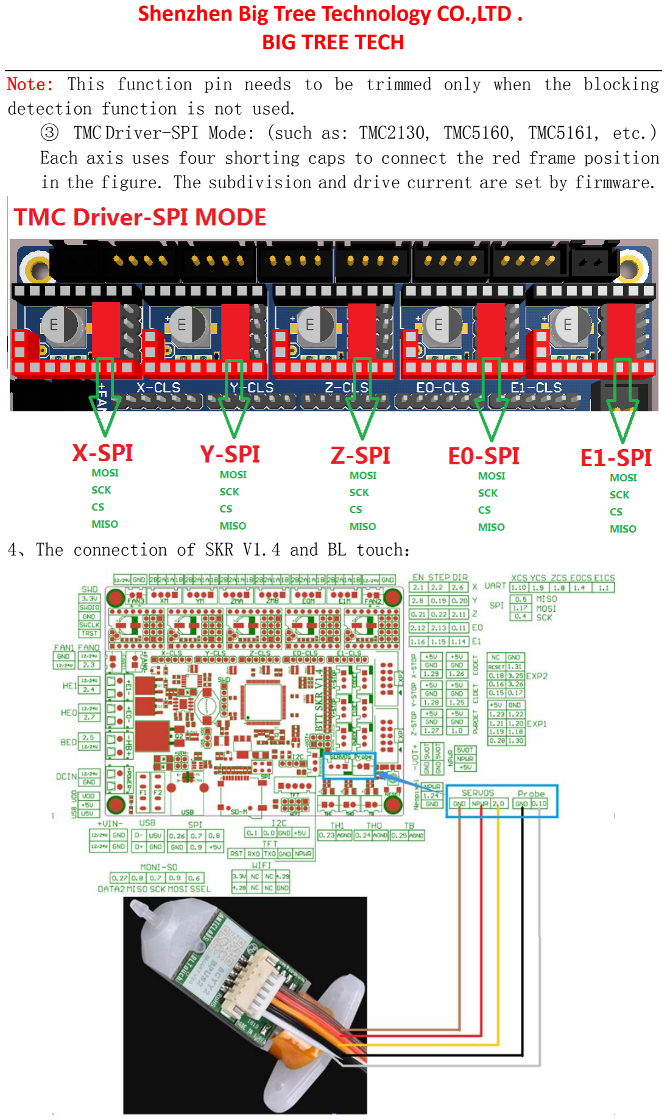
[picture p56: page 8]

Note: This function pin needs to be trimmed only when the blocking detection function is not used.
③ TMC Driver-SPI Mode: (such as: TMC2130, TMC5160, TMC5161, etc.) Each axis uses four shorting caps to connect the red frame position in the figure. The subdivision and drive current are set by firmware.

4、The connection of SKR V1.4 and BL touch：

## BIG TREE TECH

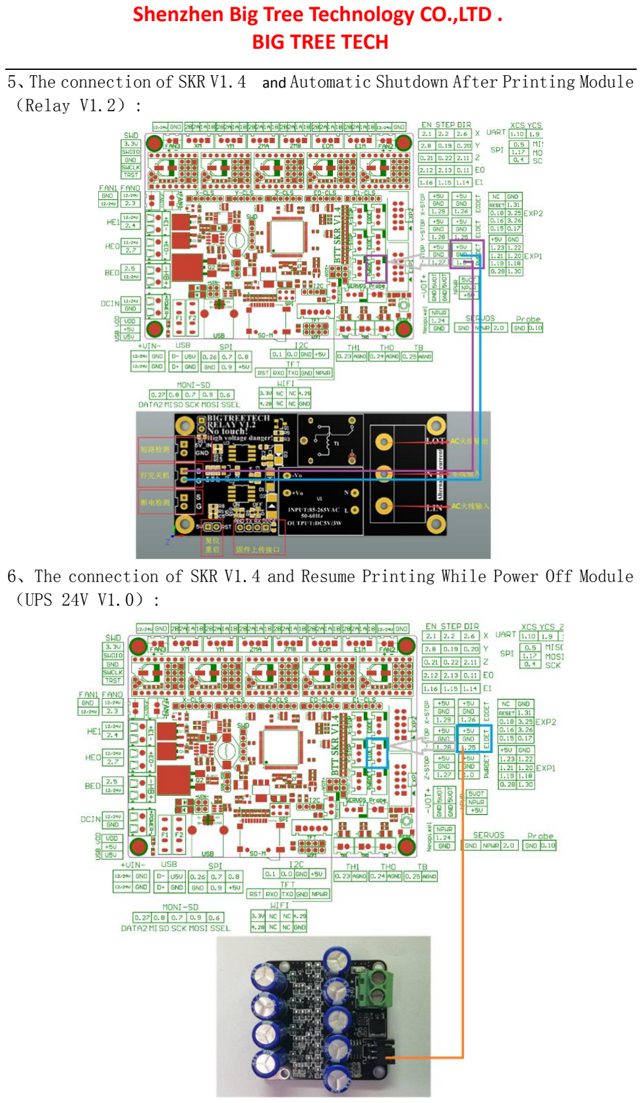
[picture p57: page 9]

5、The connection of SKR V1.4 and Automatic Shutdown After Printing Module （Relay V1.2）:

6、The connection of SKR V1.4 and Resume Printing While Power Off Module （UPS 24V V1.0）:

## BIG TREE TECH

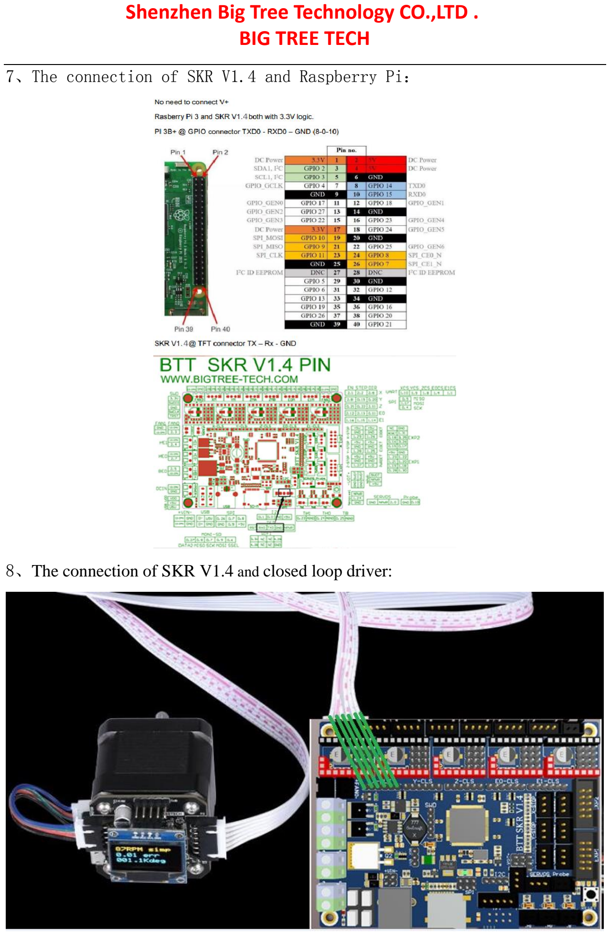
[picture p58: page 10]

7、The connection of SKR V1.4 and Raspberry Pi：

8、The connection of SKR V1.4 and closed loop driver:

## BIG TREE TECH

# Ⅴ.The firmware description of SKR

# motherboard

The factory motherboard is installed equipped with firmware for testing (model I3), which can be used directly or changed according to your own needs.
1. The Firmware Acquisition Method of SKR Motherboard:
Obtain by Ask customer service or technical personnel;
Download at our Company Open source website: https://github.com/bigtreetech
2.Marlin2.0 Firmware update method

After downloading our open source Marlin2.0 firmware, use Visual Studio Code to open the project to compile, then find the firmware.bin file, copy it to the SD card, and then reset the motherboard. For detailed steps, please refer to the tutorial:

https://www.dropbox.com/s/ppjfflhf3j5yzh2/MarlinV2.0%20SKRV1.1%20instruction.docx?dl=0

## Ⅵ.Notes：

### 1. The motherboard 5V SEL must connect VDD and +5V two pins

### before printing (that is, 12v-24v power supply must be provided

to the motherboard for printing);

### 2. The power of the hot bed connected to the motherboard must

### be less than or equal to 144W (that is, the thermal bed

### resistance is greater than 1Ω). If you want to use a high-power

### hot bed, you must connect an external hot-bed power expansion

board;

### 3. Firmware file names in SD card cannot be changed

### (including letter case)；

### 4. The wiring process and plug-in drive process must be

## BIG TREE TECH

### carried out under the premise of power failure. The power can

### be put on after checking the correct connection of the line and

### the correct insertion of the drive, so as to prevent the wrong

### connection line from burning the motherboard and driver and

### causing unnecessary losses；

### 5. To replace the configuration file, please backup the

### factory configuration file to record the pin number of each part

### of the chip, and then change the new configuration file!

### If you encounter other problems, please contact us. We will

### definitely answer your questions patiently. If you have any good

### suggestions on our products, please give us feedback. We will

### consider them seriously. Thank you for choosing BIGTREETECH

### products!

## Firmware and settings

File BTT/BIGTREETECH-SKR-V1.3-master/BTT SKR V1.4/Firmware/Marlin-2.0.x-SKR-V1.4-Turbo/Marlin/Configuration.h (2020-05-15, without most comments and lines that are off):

#pragma once
#define CONFIGURATION_H_VERSION 020000
#define STRING_CONFIG_H_AUTHOR "(none, default config)" // Who made the changes.
#define SHOW_BOOTSCREEN
#define SERIAL_PORT 0
#define SERIAL_PORT_2 -1
#define BAUDRATE 115200
  #define MOTHERBOARD BOARD_BIGTREE_SKR_V1_4_Turbo
#define EXTRUDERS 1
#define DEFAULT_NOMINAL_FILAMENT_DIA 3.0
#define TEMP_SENSOR_0 1
#define TEMP_SENSOR_1 0
#define TEMP_SENSOR_2 0
#define TEMP_SENSOR_3 0
#define TEMP_SENSOR_4 0
#define TEMP_SENSOR_5 0
#define TEMP_SENSOR_BED 1
#define TEMP_SENSOR_CHAMBER 0
#define DUMMY_THERMISTOR_998_VALUE 25
#define DUMMY_THERMISTOR_999_VALUE 100
#define MAX_REDUNDANT_TEMP_SENSOR_DIFF 10
#define TEMP_RESIDENCY_TIME     10  // (seconds) Time to wait for hotend to "settle" in M109
#define TEMP_WINDOW              1  // (°C) Temperature proximity for the "temperature reached" timer
#define TEMP_HYSTERESIS          3  // (°C) Temperature proximity considered "close enough" to the target
#define TEMP_BED_RESIDENCY_TIME 10  // (seconds) Time to wait for bed to "settle" in M190
#define TEMP_BED_WINDOW          1  // (°C) Temperature proximity for the "temperature reached" timer
#define TEMP_BED_HYSTERESIS      3  // (°C) Temperature proximity considered "close enough" to the target
#define HEATER_0_MINTEMP   5
#define HEATER_1_MINTEMP   5
#define HEATER_2_MINTEMP   5
#define HEATER_3_MINTEMP   5
#define HEATER_4_MINTEMP   5
#define HEATER_5_MINTEMP   5
#define BED_MINTEMP        5
#define HEATER_0_MAXTEMP 275
#define HEATER_1_MAXTEMP 275
#define HEATER_2_MAXTEMP 275
#define HEATER_3_MAXTEMP 275
#define HEATER_4_MAXTEMP 275
#define HEATER_5_MAXTEMP 275
#define BED_MAXTEMP      150
#define PIDTEMP
#define BANG_MAX 255     // Limits current to nozzle while in bang-bang mode; 255=full current
#define PID_MAX BANG_MAX // Limits current to nozzle while PID is active (see PID_FUNCTIONAL_RANGE below); 255=full current
#define PID_K1 0.95      // Smoothing factor within any PID loop
  #define PID_FUNCTIONAL_RANGE 10 // If the temperature difference between the target temperature and the actual temperature
  #define DEFAULT_Kp 22.2
  #define DEFAULT_Ki 1.08
  #define DEFAULT_Kd 114
#define MAX_BED_POWER 255 // limits duty cycle to bed; 255=full current
#define PREVENT_COLD_EXTRUSION
#define EXTRUDE_MINTEMP 170
#define PREVENT_LENGTHY_EXTRUDE
#define EXTRUDE_MAXLENGTH 200
#define THERMAL_PROTECTION_HOTENDS // Enable thermal protection for all extruders
#define THERMAL_PROTECTION_BED     // Enable thermal protection for the heated bed
#define THERMAL_PROTECTION_CHAMBER // Enable thermal protection for the heated chamber
#define USE_XMIN_PLUG
#define USE_YMIN_PLUG
#define USE_ZMIN_PLUG
#define ENDSTOPPULLUPS
#define X_MIN_ENDSTOP_INVERTING false // Set to true to invert the logic of the endstop.
#define Y_MIN_ENDSTOP_INVERTING false // Set to true to invert the logic of the endstop.
#define Z_MIN_ENDSTOP_INVERTING false // Set to true to invert the logic of the endstop.
#define X_MAX_ENDSTOP_INVERTING false // Set to true to invert the logic of the endstop.
#define Y_MAX_ENDSTOP_INVERTING false // Set to true to invert the logic of the endstop.
#define Z_MAX_ENDSTOP_INVERTING false // Set to true to invert the logic of the endstop.
#define Z_MIN_PROBE_ENDSTOP_INVERTING false // Set to true to invert the logic of the probe.
#define X_DRIVER_TYPE  TMC2130
#define Y_DRIVER_TYPE  TMC2130
#define Z_DRIVER_TYPE  TMC2130
#define E0_DRIVER_TYPE TMC2130
#define DEFAULT_AXIS_STEPS_PER_UNIT   { 80, 80, 400, 100 }
#define DEFAULT_MAX_FEEDRATE          { 300, 300, 5, 25 }
#define DEFAULT_MAX_ACCELERATION      { 500, 500, 100, 5000 }
#define DEFAULT_ACCELERATION          3000    // X, Y, Z and E acceleration for printing moves
#define DEFAULT_RETRACT_ACCELERATION  3000    // E acceleration for retracts
#define DEFAULT_TRAVEL_ACCELERATION   3000    // X, Y, Z acceleration for travel (non printing) moves
#define DEFAULT_EJERK    5.0  // May be used by Linear Advance
  #define JUNCTION_DEVIATION_MM 0.013 // (mm) Distance from real junction edge
#define Z_MIN_PROBE_USES_Z_MIN_ENDSTOP_PIN
#define NOZZLE_TO_PROBE_OFFSET { 10, 10, 0 }
#define MIN_PROBE_EDGE 10
#define XY_PROBE_SPEED 8000
#define Z_PROBE_SPEED_FAST HOMING_FEEDRATE_Z
#define Z_PROBE_SPEED_SLOW (Z_PROBE_SPEED_FAST / 2)
#define Z_CLEARANCE_DEPLOY_PROBE   10 // Z Clearance for Deploy/Stow
#define Z_CLEARANCE_BETWEEN_PROBES  5 // Z Clearance between probe points
#define Z_CLEARANCE_MULTI_PROBE     5 // Z Clearance between multiple probes
#define Z_PROBE_LOW_POINT          -2 // Farthest distance below the trigger-point to go before stopping
#define Z_PROBE_OFFSET_RANGE_MIN -20
#define Z_PROBE_OFFSET_RANGE_MAX 20
#define X_ENABLE_ON 0
#define Y_ENABLE_ON 0
#define Z_ENABLE_ON 0
#define E_ENABLE_ON 0 // For all extruders
#define DISABLE_X false
#define DISABLE_Y false
#define DISABLE_Z false
#define DISABLE_E false             // For all extruders
#define DISABLE_INACTIVE_EXTRUDER   // Keep only the active extruder enabled
#define INVERT_X_DIR false
#define INVERT_Y_DIR true
#define INVERT_Z_DIR false
#define INVERT_E0_DIR false
#define INVERT_E1_DIR false
#define INVERT_E2_DIR false
#define INVERT_E3_DIR false
#define INVERT_E4_DIR false
#define INVERT_E5_DIR false
#define X_HOME_DIR -1
#define Y_HOME_DIR -1
#define Z_HOME_DIR -1
#define X_BED_SIZE 200
#define Y_BED_SIZE 200
#define X_MIN_POS 0
#define Y_MIN_POS 0
#define Z_MIN_POS 0
#define X_MAX_POS X_BED_SIZE
#define Y_MAX_POS Y_BED_SIZE
#define Z_MAX_POS 200
#define MIN_SOFTWARE_ENDSTOPS
  #define MIN_SOFTWARE_ENDSTOP_X
  #define MIN_SOFTWARE_ENDSTOP_Y
  #define MIN_SOFTWARE_ENDSTOP_Z
#define MAX_SOFTWARE_ENDSTOPS
  #define MAX_SOFTWARE_ENDSTOP_X
  #define MAX_SOFTWARE_ENDSTOP_Y
  #define MAX_SOFTWARE_ENDSTOP_Z
#define HOMING_FEEDRATE_XY (50*60)
#define HOMING_FEEDRATE_Z  (4*60)
#define VALIDATE_HOMING_ENDSTOPS
#define EEPROM_CHITCHAT       // Give feedback on EEPROM commands. Disable to save PROGMEM.
#define HOST_KEEPALIVE_FEATURE        // Disable this if your host doesn't like keepalive messages
#define DEFAULT_KEEPALIVE_INTERVAL 2  // Number of seconds between "busy" messages. Set with M113.
#define BUSY_WHILE_HEATING            // Some hosts require "busy" messages even during heating
#define PREHEAT_1_LABEL       "PLA"
#define PREHEAT_1_TEMP_HOTEND 180
#define PREHEAT_1_TEMP_BED     70
#define PREHEAT_1_FAN_SPEED     0 // Value from 0 to 255
#define PREHEAT_2_LABEL       "ABS"
#define PREHEAT_2_TEMP_HOTEND 240
#define PREHEAT_2_TEMP_BED    110
#define PREHEAT_2_FAN_SPEED     0 // Value from 0 to 255
#define PRINTJOB_TIMER_AUTOSTART
#define LCD_LANGUAGE en
#define DISPLAY_CHARSET_HD44780 JAPANESE
#define LCD_INFO_SCREEN_STYLE 0
#define SDSUPPORT
#define REPRAP_DISCOUNT_FULL_GRAPHIC_SMART_CONTROLLER
#define SOFT_PWM_SCALE 0
#define SERVO_DELAY { 300 }

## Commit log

2020-03-26 Y-Axel-Bearing v. 003
    [Y-Axel-Bearing_003.FCStd, Y-Axel-Bearing_003.stl]
2020-03-28 007b stl
    [Y-Axel-Bearing_007b.stl]
2020-03-29 Y-Axel Foto
    [Y-Axel-Bearing_007a.FCStd, Y-Axel-Bearing_007a.stl, Y-Axel-Bearing_007b.FCStd]
2020-03-29 z_axel foto add
    [Afstandstykke_2mm.FCStd, Y-Axel-Bearing_003.FCStd, Y-Axel-Bearing_003.stl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]
2020-04-05 readme opdateret
    [X-Axel-Battery-Dummy.FCStd, X-Axel-Bearing_001a.FCStd, X-Axel-Bearing_001a.stl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]
2020-04-06 heated bed
2020-04-07 DragChain 22.5
    [DragChainBund_22.5.FCStd, DragChainBund_22.5.stl, DragChainTop_001.FCStd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]
2020-04-07 stl fil
2020-04-07 stl file
2020-04-07 stl foæe
2020-04-08 Stl & FreeCad filer
2020-04-12 arbejde mad printbed
    [150x150_Trekant.stl, 150x150_trekant.FCStd, 265x190_Trekant.stl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]
2020-04-13 Heatbed changes
    [Z-Axel-Bearing_020.FCStd, Z-Axel-Bearing_020.stl, Z-Axel-Bearing_030.FCStd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]
2020-04-13 Z-Axel Heatbed
    [Z-Axel-Bearing_032a.FCStd, Z-Axel-Bearing_032a.stl]
2020-04-15 Opdateringer af #d print
    [GearAxel.FCStd, GearAxel.stl, GearHolderBottom_001.FCStd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]
2020-04-17 fejl i tegninger omkring 22 mm afstand
    [GearAxel.FCStd, GearAxel.stl, GearHolderBottom_001.FCStd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]
2020-04-18 Item 0.0.570.09
    [Z-KP08_Holder_100x.stl, Z-KP08_Holder_1010.FCStd, Z-KP08_Holder_1010.stl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]
2020-04-18 3D print Foto tilføjet
    [Z-Axel-Bearing_1001b.FCStd]
2020-04-18 Nye tegninger til Z-axel
    [Z-Axel-Bearing_1010a.FCStd, Z-Axel-Bearing_1010b.FCStd, Z-Bracket_1001.FCStd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]
2020-04-18 Z-Motor_Holder Opdateret
    [Z-Bracket_1001.FCStd, Z-Motor.FCStd, Z-Motor.stl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]
2020-04-22 Video tilføjet
    [X-Axel-Printhead-Base_0100.FCStd, Z-Axel-Bearing_1000a.FCStd, Z-Axel-Bearing_1000a.stl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]
2020-04-28 hotend magneter
    [2020Cornor.FCStd, 2020Cornor.stl, 2020_Samling.FCStd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]
2020-04-29 hotbed ændringer
    [X-Axel-Bearing_1000.FCStd, X-Axel-Bearing_1000_001.stl, X-Axel-Bearing_1000_002.stl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]
2020-04-30 magnet opdatering
    [X-Axel-Bearing_1000.FCStd, X-Axel-Bearing_1000_003.stl]

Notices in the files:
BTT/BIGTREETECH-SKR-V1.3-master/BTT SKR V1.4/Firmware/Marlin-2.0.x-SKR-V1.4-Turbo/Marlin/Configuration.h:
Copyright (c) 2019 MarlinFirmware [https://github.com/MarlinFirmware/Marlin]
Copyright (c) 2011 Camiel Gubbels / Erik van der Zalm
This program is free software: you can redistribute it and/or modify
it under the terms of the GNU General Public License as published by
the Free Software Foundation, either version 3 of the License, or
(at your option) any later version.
